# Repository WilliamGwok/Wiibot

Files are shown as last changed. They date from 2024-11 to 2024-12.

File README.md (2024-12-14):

### English Version Please Click: [ENG_README](https://github.com/WilliamGwok/Wiibot/blob/main/README_ENG.md)

### 日本語翻訳版: [JAP_README](https://github.com/WilliamGwok/Wiibot/blob/main/README_JAP.md)

# Wiibot

## 前言
<div align="center">
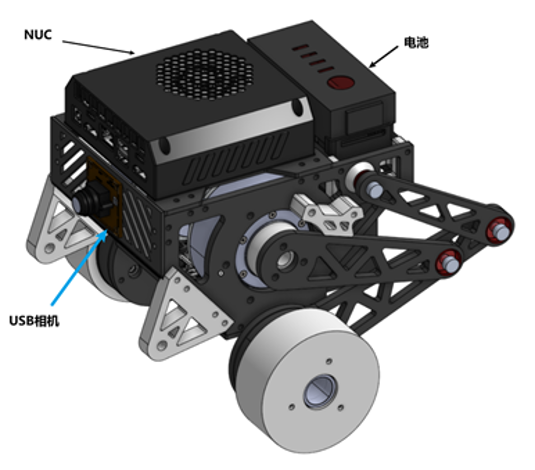
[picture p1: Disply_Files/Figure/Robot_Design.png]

</div>
<br>
<p align="center">本项目是选修机器人控制课程的课程设计，主要研究平衡车的控制与设计。该项目与先前的RP_Balance项目相似，但采用了不同的腿部构型，并保留了更多测试数据以支持研究分析。</p>
<p align="center">机器人机械部分由RobotPilots实验室的同事ZJH负责，视觉识别部分由ZZ负责。</p>

## 电控硬件清单
| 名称 | 部分技术参数 | 功能 | 数量 |
|---|---|---|---|
| Robomaster 开发板 C 型 | 输入电压: 8-28 V<br>IMU+E-compass: 1 个<br>CAN 总线接口: CAN1: 2 个; CAN2: 2 个<br>UART 接口: 2 个<br>SPI 接口: 1 个 | 搭载高性能芯片，支持机器人控制频率达 1000Hz，同时负责电机通讯、遥控信息接收及视觉模块通信。 | 1 |
| 迈克 mc6mini 遥控器航模接收机 | 通道数量: 6<br>频率范围: 2401-2478 MHz<br>控制范围: >800 m | 发送机器人平移、旋转、跳跃等动作指令。 | 1 |
| 领控 MG6012E-i8v3 伺服电机 | 额定电压: 48 V<br>空载转速: 310 rpm<br>额定扭矩: 6 Nm<br>峰值扭矩: 16 Nm | 控制机器人腿长及机体横滚角。 | 2 |
| Robomater GM6020 电机 | 额定电压: 24 V<br>空载转速: 320 rpm<br>额定扭矩: 1.2 Nm<br>峰值扭矩: 1.4 Nm  | 控制机器人驱动轮，实现平移、旋转及平衡。 | 2 |
| 经纬 M600 系列 TB47S 智能飞行电池 | 容量: 4500 mAh<br>电压: 22.2 V | 提供整套机器人的电控系统供电。 | 1 |
| DC-DC 可调电源模块 | 输入电压: 7-32 V<br>输出电压: 0-28 V<br>恒流范围: 0.2-1.2 A | 为视觉NUC提供稳定的工作电压与电流。 | 1 |

## 文件介绍

| 文件名 | 功能 | 文件链接 |
|---|---|---|
| Code | 包括MATLAB代码（建模求解、控制器设计、增益矩阵拟合、数据绘制）和实车代码（硬件驱动、通讯协议、模块控制与逻辑控制）。 | [CODE](https://github.com/WilliamGwok/Wiibot/tree/main/Code) |
| Display_Files | 机械、电控、视觉课程报告及演示文件。 | [DISPLAY](https://github.com/WilliamGwok/Wiibot/tree/main/Disply_Files) |
| Mec | 包含机器人机械设计图纸。 | [MEC](https://github.com/WilliamGwok/Wiibot/tree/main/Mec/balance) |
| Simulation | Webots平台的机器人仿真模型*。 | [SIM](https://github.com/WilliamGwok/Wiibot/tree/main/Simulation/webots) |
| Test_Video | 包含实车测试图片及视频文件。 | [VIDEO](https://github.com/WilliamGwok/Wiibot/tree/main/Test_Video) |

*由于导入STL文件到Webots平台较为复杂，简化模型后仿真世界仍难以正常运行。最终仅验证了机器人维持平衡的功能。

## 实车测试

对整车控制器性能进行了测试与分析。除腿长控制器和横滚角控制器的测试外，其他测试均在固定腿长的条件下进行。对应的增益矩阵K如下，所有数据通过J-Scope测量，并使用MATLAB绘制：

$$
K={\left[\begin{array}{l l l l l l}{-3.693}&{-3.287}&{-8.559}&{-0.591}&{3.693}&{0.369; }\\ {-3.693}&{-3.287}&{-8.559}&{-0.591}&{-3.693}&{-0.369}\end{array}\right]}
$$

### 平衡车位移、偏航角静态响应及俯仰角变化

在静止状态下，输入幅值为0.4的阶跃信号，测试机器人位移响应及俯仰角变化，结果如图1所示。

<div align="center">
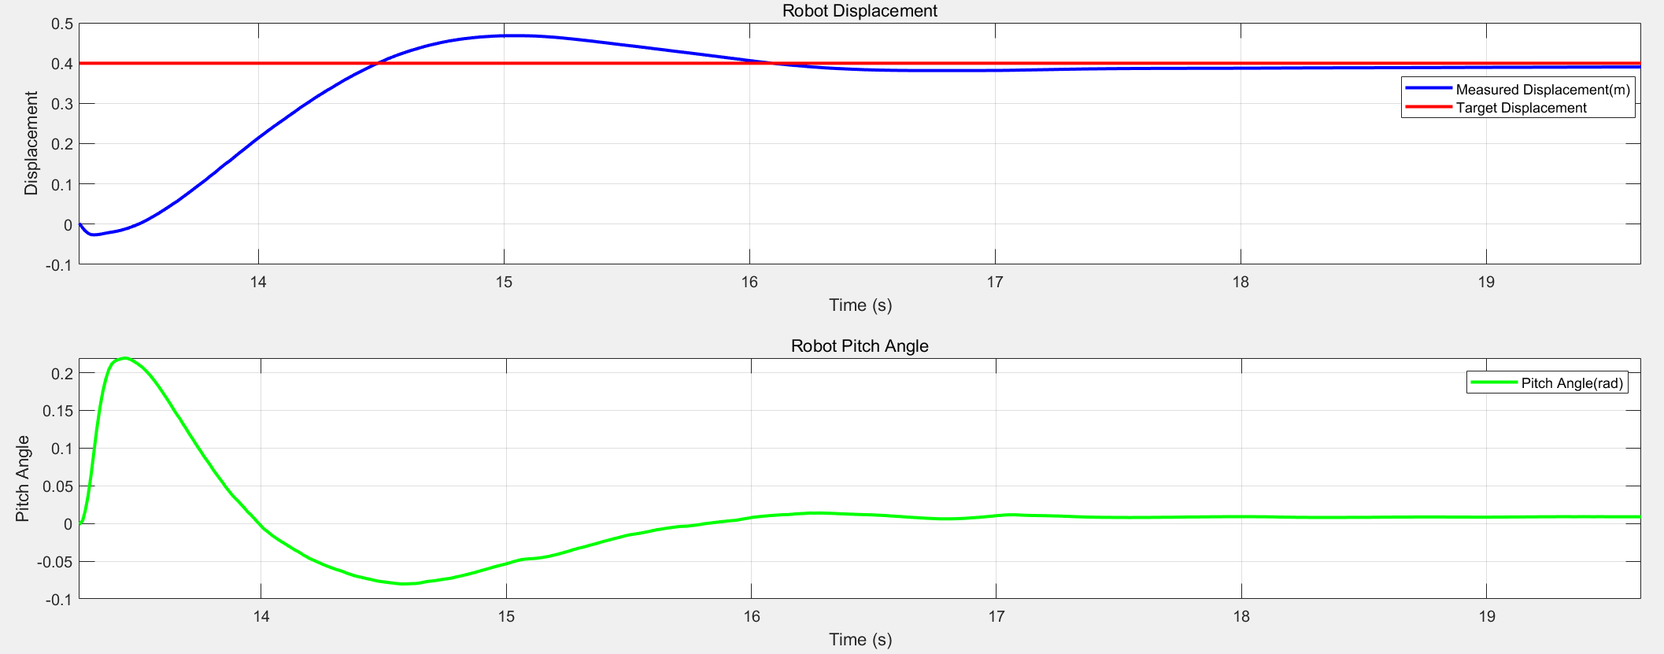
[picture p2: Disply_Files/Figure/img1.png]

</div>
<br>
<p align="center">图1 机器人位移阶跃响应及其俯仰角变化</p>

经测量，位移响应特性如下：

- 峰值时间 $T_{P}$：1.731s
- 超调量 $\upsigma\%$：17\%
- 调节时间 $T_{S}$（5%误差下）：2.542s

位移响应过程中，机器人最大俯仰角为0.219 rad（约12.549度）。

在静止状态下，输入幅值为1.579（约90度）的偏航角阶跃信号，测试偏航角响应及俯仰角变化，结果如图2所示。

<div align="center">
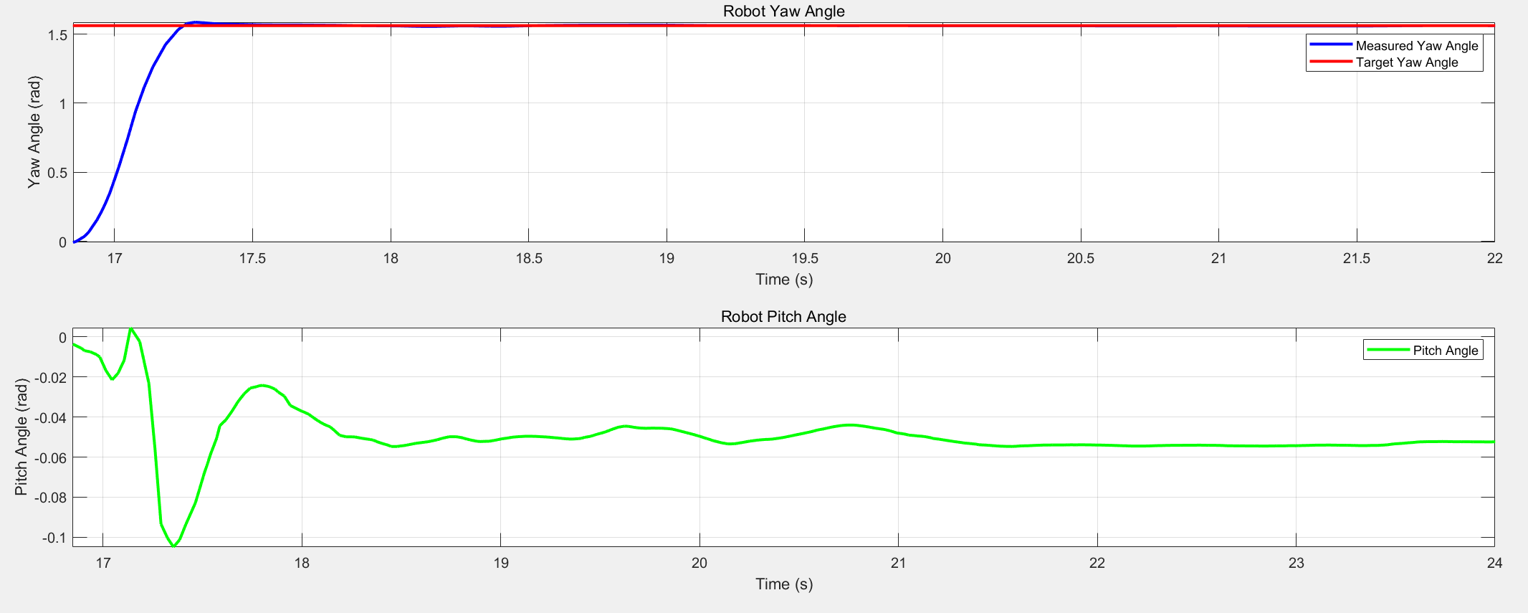
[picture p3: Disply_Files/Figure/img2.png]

</div>
<br>
<p align="center">图2 机器人偏航角阶跃响应及其俯仰角变化</p>

偏航角响应特性如下：

- 峰值时间 $T_{P}$：0.477s

- 超调量 $\upsigma\%$：1.6\%

- 调节时间 $T_{S}$（5%误差下）：0.385s

偏航角轨迹跟踪过程中，俯仰角在0.104 rad内产生小幅度震荡。

### 平衡车腿长及机体横滚角响应

采用双环PID控制器对腿长进行控制。输入幅值为0.3的阶跃信号，位置外环与速度内环响应如图3所示。

控制器参数如下：

$$
\begin{array}{l}{{K p=100,\qquad K i=0.5,\qquad I n t e r g r a l_{m a x}=10,\qquad O u t_{m a x}=30;}}\\ {{\mathrm{}}}\\ {{\mathrm{}\kappa p=0.4,\qquad K i=0.05,\qquad I n t e r g r a l_{m a x}=5,\qquad O u t_{m a x}=8;}}\end{array}
$$

<div align="center">
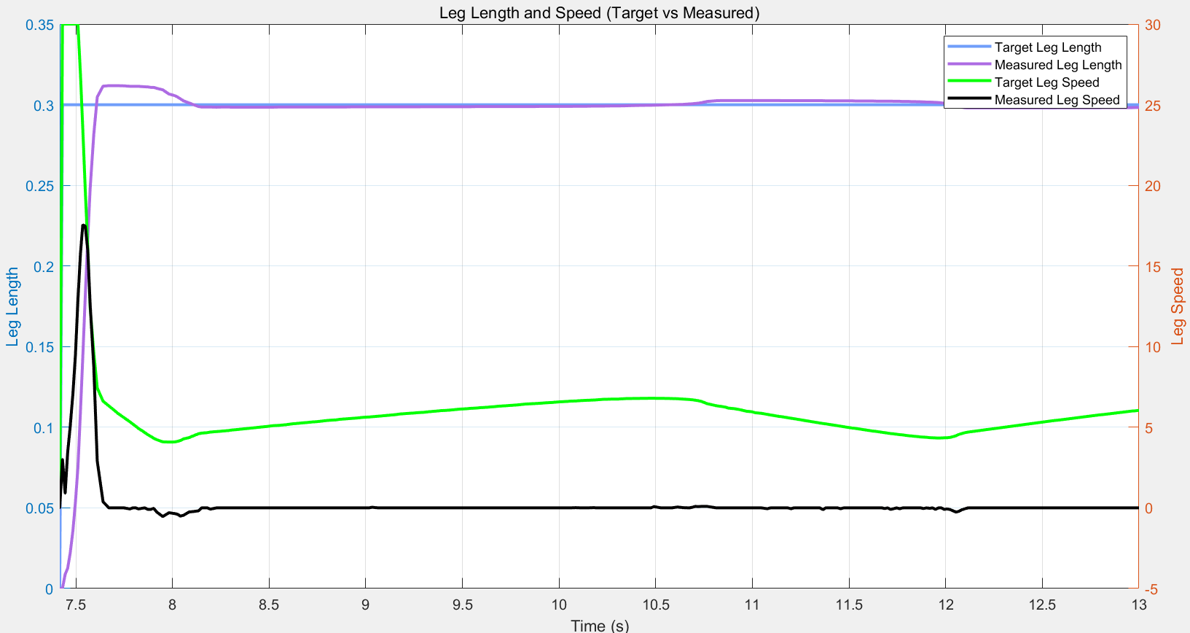
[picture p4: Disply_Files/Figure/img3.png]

</div>
<br>
<p align="center">图3 机器人腿长双环控制器响应</p>

再次输入最大腿长阶跃信号，响应如图4所示。

<div align="center">
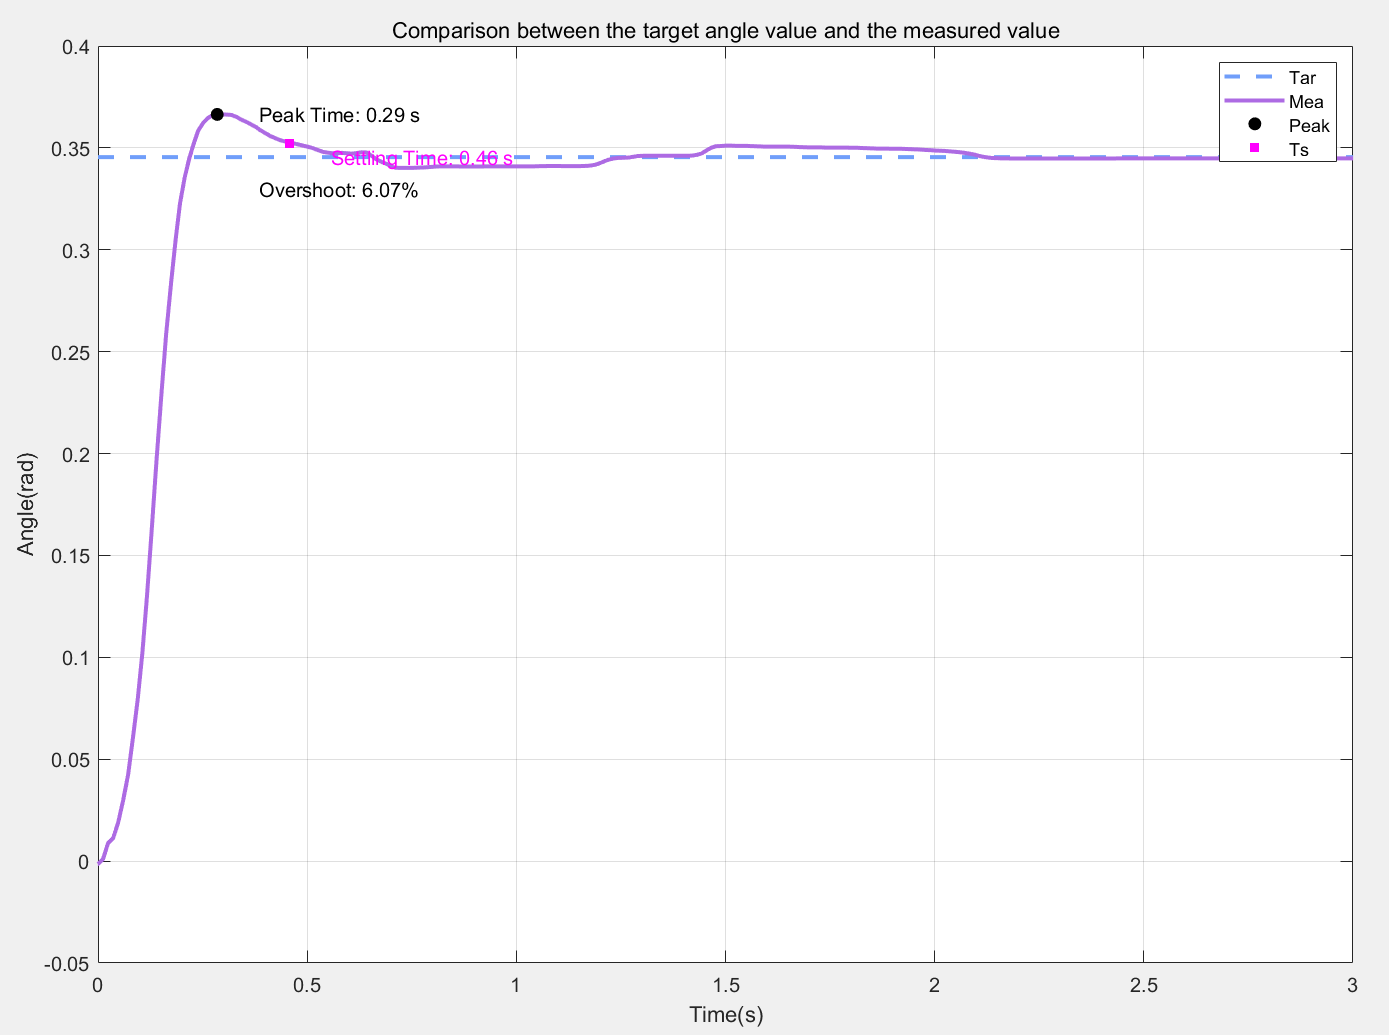
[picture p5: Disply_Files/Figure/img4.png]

</div>
<br>
<p align="center">图4 机器人腿长最大阶跃响应</p>

经测量，腿长响应特性如下：

- 峰值时间 $T_{P}$：0.29s

- 超调量 $\upsigma\%$：6.07\%

- 调节时间 $T_{S}$（2%误差下）：0.46s

横滚角响应通过单侧上坡动作*体现，其横滚角及左右腿腿长变化如图5所示。

<div align="center">
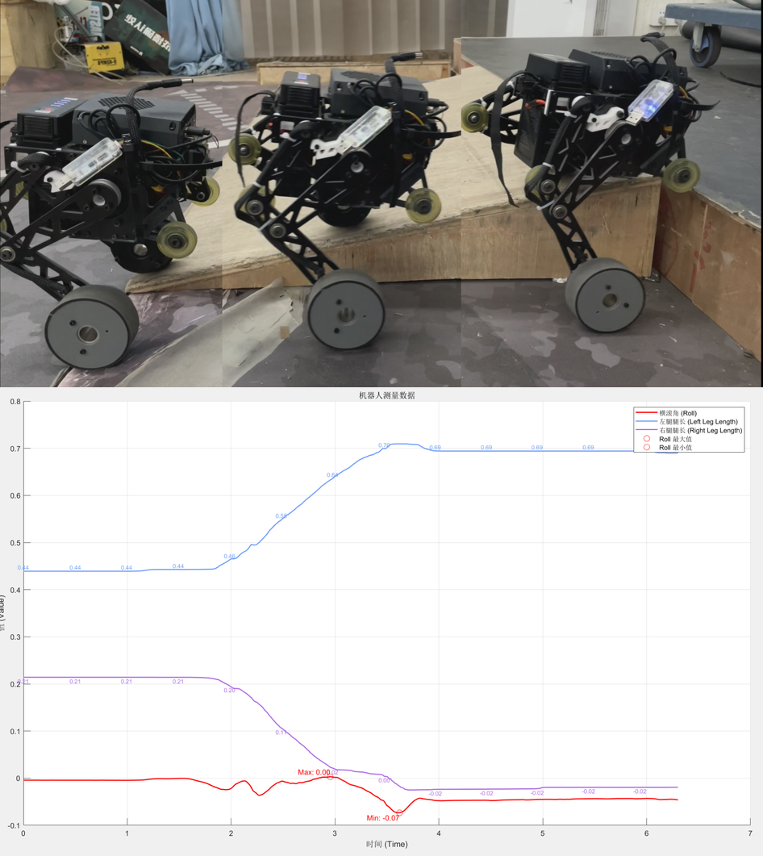
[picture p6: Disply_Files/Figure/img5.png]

</div>
<br>
<p align="center">图5 单侧上坡时横滚角与腿长变化</p>

*上坡过程持续2s，坡长约0.8m，坡度9 °

### 离地检测与跳跃动作

通过监测关节扭矩检测离地状态。图6展示了两次离地的关节扭矩输出曲线，设置离地阈值为0.5Nm，经测试可靠性较高。

<div align="center">
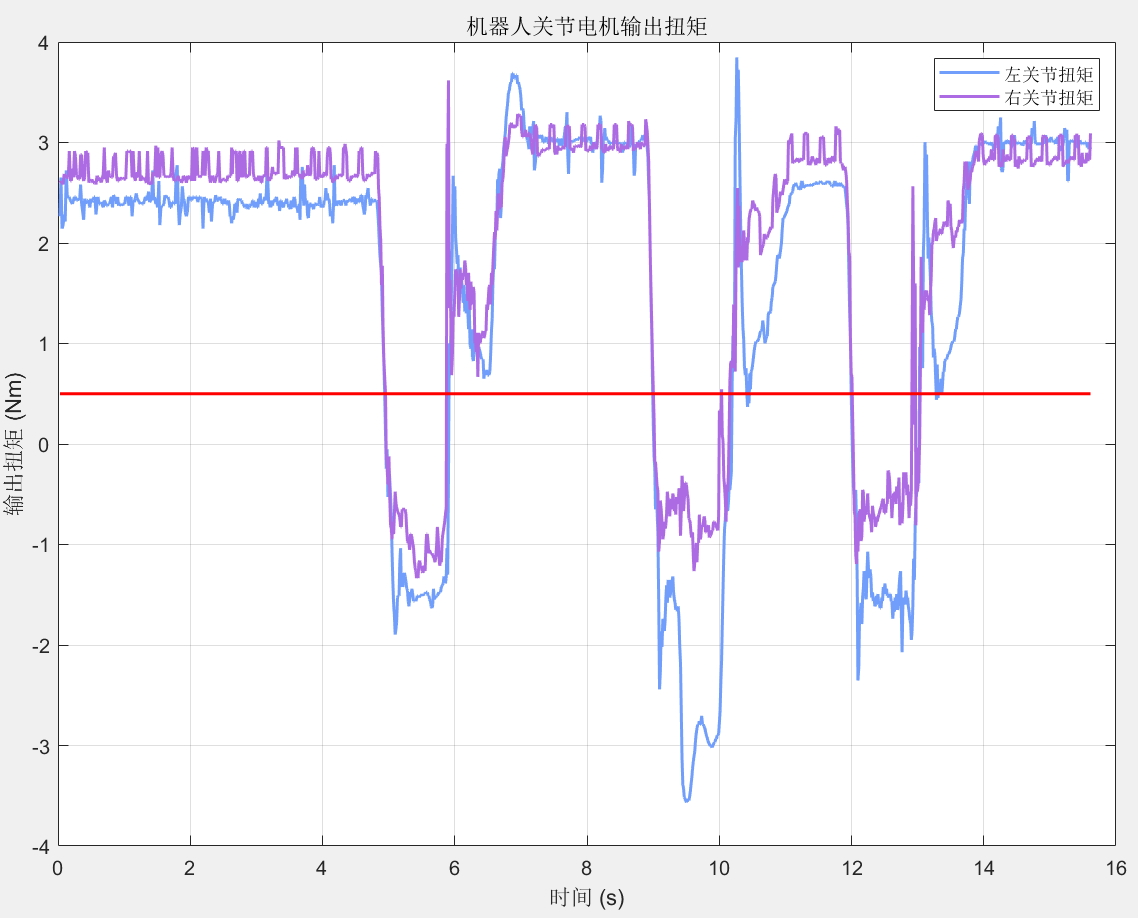
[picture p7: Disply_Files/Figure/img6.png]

</div>
<br>
<p align="center">图6 离地检测扭矩曲线</p>

通过给腿长输入大幅脉冲信号实现跳跃。平均跳跃高度约为0.1m，受限于电机性能，跳跃高度尚有改进空间。跳跃时的控制器输出如图7和图8所示。

<div align="center">
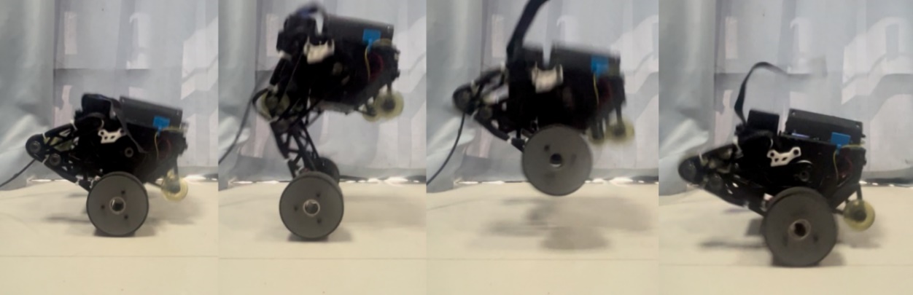
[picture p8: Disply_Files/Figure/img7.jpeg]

</div>
<br>
<p align="center">图7 跳跃过程</p>

<div align="center">
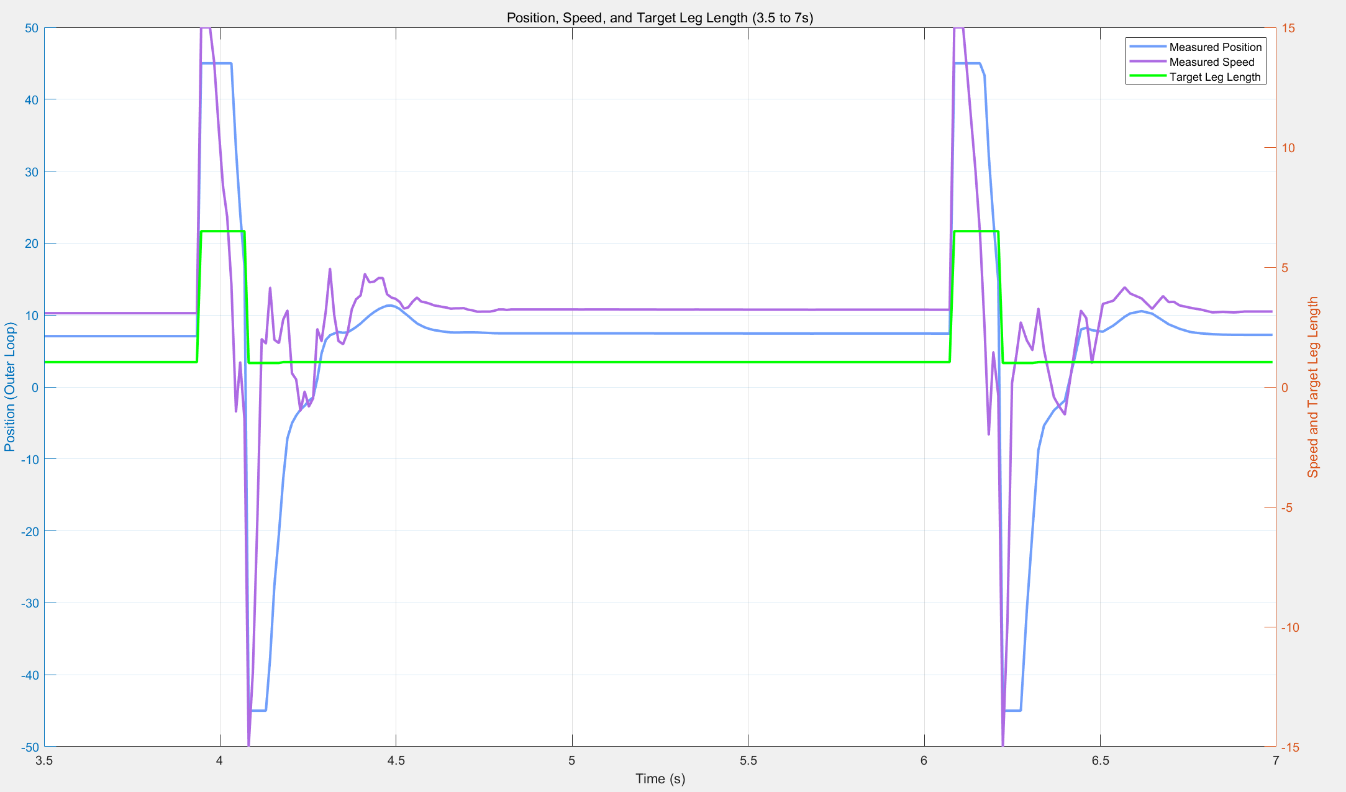
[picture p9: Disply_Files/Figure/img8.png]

</div>
<br>
<p align="center">图8 跳跃动作控制器输出曲线</p>

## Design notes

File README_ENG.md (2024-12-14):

# Wiibot

## Preface
<div align="center">

</div>
<br>
<p align="center">This project is part of the coursework for the Robotics Control course, focusing on the control and design of a balance robot. It is similar to the previous RP_Balance project but adopts a different leg configuration and retains more test data to support research and analysis.</p>
<p align="center">The mechanical components of the robot were designed by ZJH from the RobotPilots lab, while the visual recognition module was handled by ZZ.</p>

## Electronic Hardware List
| Name | Technical Specifications | Function | Quantity |
|---|---|---|---|
| Robomaster Development Board Type C | Input Voltage: 8-28 V<br>IMU+E-compass: 1<br>CAN Bus: CAN1: 2 ports; CAN2: 2 ports<br>UART Ports: 2<br>SPI Port: 1 | Supports high-performance chip with control frequency up to 1000Hz; handles motor communication, remote control signal reception, and vision module communication. | 1 |
| Mike MC6mini Remote Control Receiver | Channels: 6<br>Frequency Range: 2401-2478 MHz<br>Control Range: >800 m | Sends commands for robot translation, rotation, and jumping actions. | 1 |
| Lingkong MG6012E-i8v3 Servo Motor | Rated Voltage: 48 V<br>No-load Speed: 310 rpm<br>Rated Torque: 6 Nm<br>Peak Torque: 16 Nm | Controls leg length and robot body roll angle. | 2 |
| Robomater GM6020 Motor | Rated Voltage: 24 V<br>No-load Speed: 320 rpm<br>Rated Torque: 1.2 Nm<br>Peak Torque: 1.4 Nm | Drives the robot wheels for translation, rotation, and balance. | 2 |
| DJI M600 TB47S Intelligent Flight Battery | Capacity: 4500 mAh<br>Voltage: 22.2 V | Provides power for the entire robot control system. | 1 |
| DC-DC Adjustable Power Module  | Input Voltage: 7-32 V<br>Output Voltage: 0-28 V<br>Constant Current Range: 0.2-1.2 A | Supplies stable voltage and current to the vision NUC. | 1 |

## File Overview

| Filename | Function | File Link |
|---|---|---|
| Code | Includes MATLAB code (modeling, controller design, gain fitting, data plotting) and real robot code (hardware drivers, communication protocols, module control, and logic control). | [CODE](https://github.com/WilliamGwok/Wiibot/tree/main/Code) |
| Display_Files  | Reports and presentation files on mechanics, electronics, and vision. | [DISPLAY](https://github.com/WilliamGwok/Wiibot/tree/main/Disply_Files) |
| Mec | Contains mechanical design drawings of the robot. | [MEC](https://github.com/WilliamGwok/Wiibot/tree/main/Mec/balance) |
| Simulation | Robot simulation models for the Webots platform.* | [SIM](https://github.com/WilliamGwok/Wiibot/tree/main/Simulation/webots) |
| Test_Video | Includes real robot test images and videos. | [VIDEO](https://github.com/WilliamGwok/Wiibot/tree/main/Test_Video) |

*Due to the complexity of importing STL files into the Webots platform, the simplified model still struggled to function properly in the simulation environment. Only balance maintenance was verified.

## Real Robot Tests

The performance of the overall controller was tested and analyzed. Except for the leg length controller and roll angle controller tests, other tests were conducted under fixed leg length conditions. The corresponding gain matrix K is shown below. All data was measured with J-Scope and plotted using MATLAB:

$$
K={\left[\begin{array}{l l l l l l}{-3.693}&{-3.287}&{-8.559}&{-0.591}&{3.693}&{0.369; }\\ {-3.693}&{-3.287}&{-8.559}&{-0.591}&{-3.693}&{-0.369}\end{array}\right]}
$$

### Balance Robot Displacement, Yaw Angle Static Response, and Pitch Angle Variation

In a stationary state, an input step signal with an amplitude of 0.4 was applied to test the robot's displacement response and pitch angle variation. The results are shown in Figure 1.

<div align="center">

</div>
<br>
<p align="center">Figure 1 Displacement Step Response and Pitch Angle Variation</p>

The measured displacement response characteristics are as follows:

- Peak Time $T_{P}$: 1.731s
- Overshoot $\upsigma\%$: 17%
- Settling Time $T_{S}$ (within 5% error): 2.542s

During the displacement response, the maximum pitch angle was 0.219 rad (approximately 12.549 degrees).

Under stationary conditions, an input yaw step signal with an amplitude of 1.579 (approximately 90 degrees) was applied to test the yaw response and pitch angle variation. The results are shown in Figure 2.

<div align="center">

</div>
<br>
<p align="center">Figure 2 Yaw Step Response and Pitch Angle Variation</p>

Yaw response characteristics are as follows:

- Peak Time $T_{P}$: 0.477s

- Overshoot $\upsigma\%$: 1.6%

- Settling Time $T_{S}$ (within 5% error): 0.385s

During yaw trajectory tracking, the pitch angle oscillated slightly within 0.104 rad.

### Balance Robot Leg Length and Body Roll Angle Response

A dual-loop PID controller was used for leg length control. When a step signal with an amplitude of 0.3 was applied, the outer position loop and inner velocity loop responses are shown in Figure 3.

Controller parameters:

$$
\begin{array}{l}{{K p=100,\qquad K i=0.5,\qquad I n t e r g r a l_{m a x}=10,\qquad O u t_{m a x}=30;}}\\ {{\mathrm{}}}\\ {{\mathrm{}\kappa p=0.4,\qquad K i=0.05,\qquad I n t e r g r a l_{m a x}=5,\qquad O u t_{m a x}=8;}}\end{array}
$$

<div align="center">

</div>
<br>
<p align="center">Figure 3 Leg Length Dual-Loop Controller Response</p>

When the maximum leg length step signal was applied, the response is shown in Figure 4.

<div align="center">

</div>
<br>
<p align="center">Figure 4 Maximum Leg Length Step Response</p>

The measured leg length response characteristics are as follows:

- Peak Time $T_{P}$: 0.29s

- Overshoot $\upsigma\%$: 6.07%

- Settling Time $T_{S}$ (within 2% error): 0.46s

The roll angle response was demonstrated through a single-side uphill motion*, with the roll angle and left/right leg length variations shown in Figure 5.

<div align="center">

</div>
<br>
<p align="center">Figure 5 Roll Angle and Leg Length Variation During Single-Side Uphill</p>

*The uphill process lasted 2 seconds, with a slope length of approximately 0.8m and a slope angle of 9°.

### Ground Detection and Jumping Motion

Ground detection was achieved by monitoring joint torque. Figure 6 shows the torque curves for two ground detections. The threshold was set at 0.5 Nm, with high reliability observed during tests.

<div align="center">

</div>
<br>
<p align="center">Figure 6 Torque Curves for Ground Detection</p>

Jumping was implemented by inputting a large pulse signal to the leg length. The average jump height was approximately 0.1m. Limited by motor performance, the jump height has room for improvement. The controller outputs during jumping are shown in Figures 7 and 8.

<

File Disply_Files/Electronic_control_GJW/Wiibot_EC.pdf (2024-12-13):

深圳大学本科生生课程论文

1.系统建模

对于机器人的平衡，纵向以及转向运动，可以将模型简化为三维空间中的类一阶倒立摆 模型，即忽略腿长的变化，转向运动由两个驱动轮差速运动控制。

1.1 模型定义

称机器人机体质心到两个驱动轮转轴中心的连线为摆杆，得到如图 1 所示平衡车 模型。

该模型的变量与参数定义如表 1、表 2 所示。

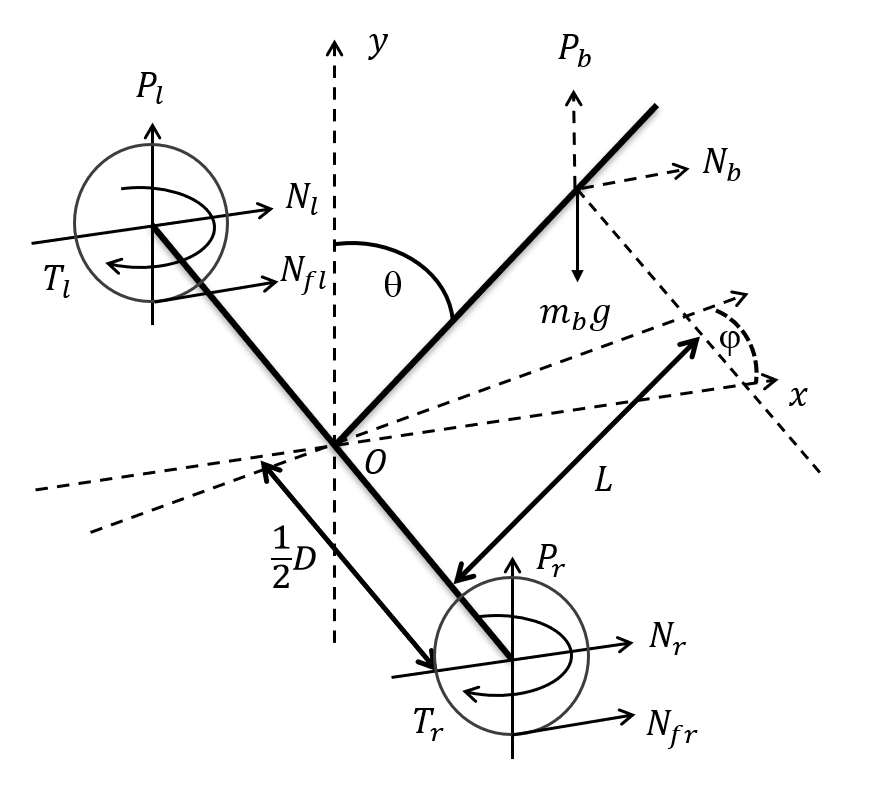
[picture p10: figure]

图 1 平衡车模型

表 1 平衡车模型变量定义

符号 | 含义 | 正方向 | 单位
θ | 摆杆与竖直方向夹角 | 图示为正方向 | rad
φ | 摆杆偏航角 | 图示为正方向 | rad
xi | 驱动轮位移 | X 轴正方向 | m
xb | 机体位移 | X 轴正方向 | m
Pi | 驱动轮对摆杆力的竖直分量 | 箭头所示 | N
Pb | 摆杆受到的竖直方向力 | 箭头所示 | N
Ni | 驱动轮对摆杆力的水平分量 | 箭头所示 | N

Nb | 摆杆受到的水平方向力 | 箭头所示 | N
Ti | 驱动轮输出力矩 | 箭头所示 | N·m

表 2 平衡车模型参数定义

符号 | 单位 | 含义
D | m | 车体转向直径
R | m | 驱动轮半径
L | m | 摆杆质心到驱动轮转轴中心的直线长度
mw | kg | 驱动轮质量
mb | kg | 摆杆质量
Ib | kg ∙ m² | 摆杆绕质心关于 Z 轴的转动惯量
Iw | kg ∙ m² | 驱动轮转子转动惯量
Iz | kg ∙ m² | 整车质心关于 Y 轴的转动惯量

1.2 经典力学分析

对驱动轮，有：

mwxi

̈ = Nfi − Ni | (1)

Iw

xi

̈
R
= Ti − NfiR | (2)

对摆杆，有：

mbxb̈ = Nfl + Nfr | (3)
mbyb̈ = Pr + Pl − mbg | (4)

Ibθb

̈ = (Pr + Pl)L sin θb − (Nr + Nl )L cos θb − (Tr + Tl) | (5)

对整车，有：

Izφ̈=

D
2
(Nl − Nr ) | (6)

其中：

xb = x + L sin θb | (7)
yb = L cos θb | (8)

1.3 状态空间模型

定义非线性模型：

ẋ = f(x, Tl

, Tr )

利用 MATLAB 符号运算工具，联立式（1）到式（8），通过函数 solve 对方程组消 去中间变量，最终得到非线性表达式（9），式（10），和式（11）

2mwẍ+ mb (ẍ− L (sin(θb) θb
̇

2
− θb

̇ cos(θb))) −

Tl
R

−

Tr
R

+

2Iwẍ
R²
= 0 | (9)

Tl + Tr + Ibθb

̈ − L sin(θb) (gmb − Lmb (cos(θb) θb ̇

2
+ θb

̈ sin(θb))) − 2Lmwẍcos(θb)

+

LTl cos(θb)
R

+

LTr ∗ cos(θb)
R

−

2IwLẍcos(θb)
R²
= 0 | (10)

DTlR = mwφb

̈D
2R

2 + Iwφb

̈D
2 + TrDR + 2Izφb

̈R
2 | (11)

定义状态向量 x 与控制向量 u 分别为：

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
φ̇ ]

, u = [

Tl
Tr

]

根据式状态向量 x 与控制向量 u，求非线性模型在平衡点处的雅可比矩阵并对其线性化，即 将θ = 0，则sin θ = θ, cos θ = 1代入式（9）到（11）后，求：

A =

∂f
∂x (x, u), B =

∂f
∂u (x, u)

其中，x、u 是系统平衡点，即方程f(x, u) = 0的解：

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
, u = [

0/0]

最终求得的状态方程为：

ẋ =
[
0 1 | 0 | 0 | 0 0
0 0 A1 | A2 | 0 0
0 0 | 0 | 1 | 0 0
0 0 A3 | A4 | 0 0
0 0 | 0 | 0 | 0 1
0 0 | 0 | 0 | 0 0]

x +
[
0 | 0
B1 | B2
0 | 0
B3 | B4
0 | 0
B5 | B6]
u | (12)

由于表达式略为复杂，此处用符号代替，具体内容可通过运行 MATLAB 代码在工作空间中 查看。

所有变量均可通过平衡车上各个传感器（如驱动轮编码器，IMU 模块等）直接测量或通过数 据融合解算得到，故可得系统输出y = I6x，其中I6为单位阵。

代入平衡车实车模型参数后可以得到该状态空间模型的状态矩阵 A 和控制矩阵 B，在 MATLAB 中使用 rank 函数求得其可控矩阵满秩，系统可控。系统输出矩阵 C 为单位矩阵， 系统可观。

1.4 仿真验证

将 Solidwork 中搭建的模型分模块导入到仿真软件 Webots 中，通过对关节电机设置其允许 位移为 0，得到一个定腿长的平衡车模型。

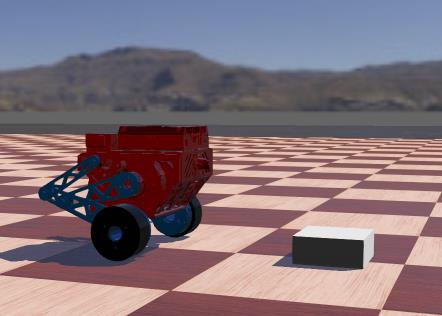
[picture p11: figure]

图 2 仿真环境中的整车模型

通过使用 MATLAB 中的 lqr 函数计算得到反馈增益矩阵 K。因为在仿真中主要目的是验证 模型建立是否正确，用于计算 K 矩阵的 Q 和 R 权矩阵的数值选取只关注机器人俯仰角的稳 定。经检验，得到模型正确。

2 控制器设计

基于本项目的平衡车构型，除了机器人的平移、转向和保持平衡的控制外，还需要控制 平衡车双腿的长度及其横滚角。

2.1 LQR 控制器

基于上述求得的状态空间方程，通过一个 LQR 控制器可以较好地对机器人平移、旋转 以及机体俯仰角进行控制。

设计控制律为系统状态的线性组合：

u = −Kx = − [

K11 | K12 | K13 | K14 | K15 | K16
K21 | K22 | K23 | K24 | K25 | K26

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
φ̇ ]

通过线性二次型调节器计算反馈矩阵，定义代价函数为

J = ∫ (x
TQx + u

TRu)dt

∞

0
其中：
- x 是系统状态向量；
- u是控制输入向量；
- Q 是对状态变量的加权矩阵，通常是半正定矩阵，反映了对状态偏离的惩罚；
- R是对控制输入的加权矩阵，通常是正定矩阵，反映了对控制能量的惩罚。

最优控制律：

为了使代价函数J达到最小，控制输入 u 应满足以下关系：

u = −R

−1B

TPx

其中：

- P是代数 Riccati 方程的解。

反馈增益矩阵：

通过上述控制律，反馈增益矩阵 K可以表示为：

K = R

−1B

TP

代数 Riccati 方程:

矩阵P需要满足以下代数 Riccati 方程：

A

TP + PA − PBR

−1B

TP + Q = 0

其中：

- A 和 B 是系统状态空间方程中的系统矩阵和输入矩阵。

为了可以控制平衡车的移动和转向，还需要实现对位移和偏航角两个状态变量的轨迹跟 踪。在系统输入中加入参考输入，即状态期望：

u = −K(x − xd)

其中xd为：

xd =
[

xd
0
0
0
φd
0 ]

xd为期望位移，φd为期望偏航角，两者均由其期望一阶微分量对时间积分得到。

2.2 双环 PID 控制器

基于该项目平衡车的四连杆腿部构型，可以通过关节电机的输出来调整机器人的腿部长 度；同时，为了让机器人在进行视觉识别时机体保持横滚角水平，还需要根据机器人实时的 横滚角值来调整两边腿的长度。

为了让机器人的腿长控制有更快的响应速度和鲁棒性，引入两个双环 PID 控制器分别 对机器人的腿长和横滚角进行控制，最后并行输出到电机控制电流值。

腿长的控制框图如图 3 所示：

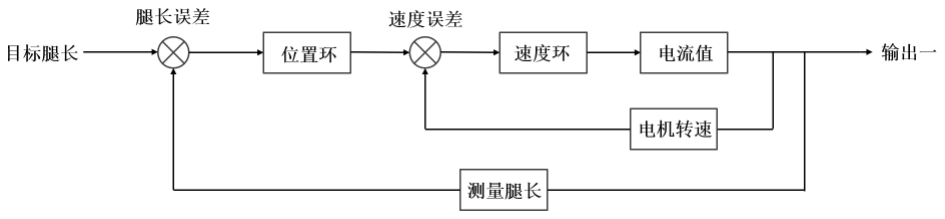
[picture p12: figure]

图 3 机器人腿长双环 PID 控制框图

横滚角的控制框图如图 4 所示：

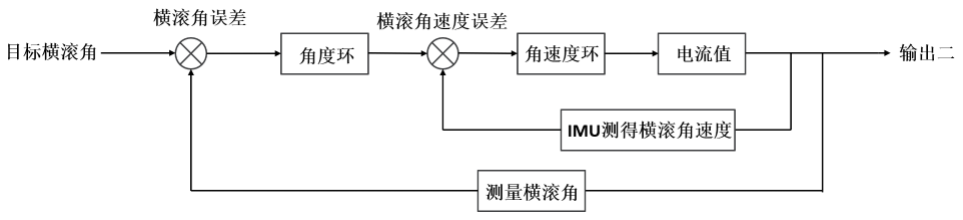
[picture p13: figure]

图 4 机器人横滚角双环 PID 控制框图

最终发送的电机电流值为两个控制器的输出之和。

2.3 增益矩阵 K 的参数拟合

在建模阶段，我们将倒立摆的杆长假设为定值，但实际上，该值会随着机器人腿长的变 化而改变，其对应的模型也会有差异。由于求得解析解较为困难，我们将机器人腿长作为拟 合的自变量，对增益矩阵 K 进行四阶多项式拟合。

由于实车环境下我们无法直接测量机器人实时腿长，需要由一些角度关系推算得到。将 模型简化至如图 5 所示。

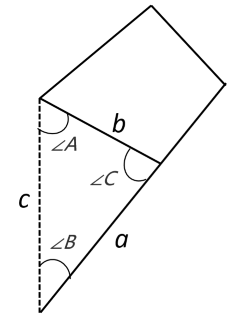
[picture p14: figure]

图 5 腿部四连杆结构简化模型

其中，三角形边 a、边 b 可以通过在机械图纸中测量得到，角 A 可以由电机编码器求 得，边 c 则是期望求得的机器人腿长。由余弦定理得式（13）：

a

2 − b

2 − c

2 + 2bc cos(A) = 0 | (13)

通过 MATLAB 的 solve 函数求解（排除负数解）得式（14）：

c = b cos(A) + √a
2 + b

2 cos²(A) − b

2 | (14)

经测量，实车边b = 0.11291m，边a = 0.11461m，将数据代入并由 0 至 90 度遍历角 A 可以得到角 A 与腿长的关系曲线如图 6 所示。

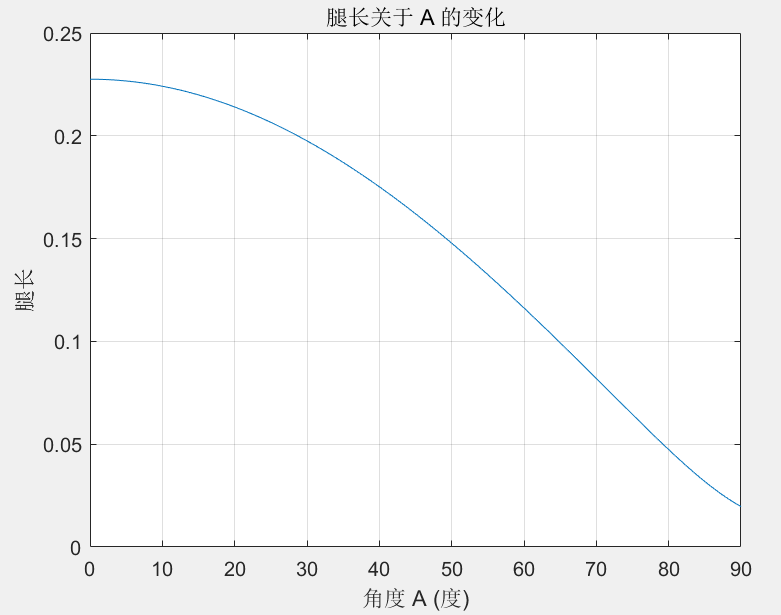
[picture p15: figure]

图 6 机器人腿长与角度 A 的关系曲线

在 MATLAB 中遍历腿长，计算不同腿长值下的增益矩阵 K，并对 K 矩阵每个元素进 行关于角度 A 的多项式拟合，求得拟合系数并存到 EXCEL 表格中，以便将它们添加进实 车代码中进行增益矩阵的实时计算。

拟合公式如式（15）：

y = a4x

4 + a3x

3 + a2x

2 + a1x + a0

其中 y 对应 K 矩阵的各个元素，x 为测得角度 A 的值。

最终的拟合效果如图 7 所示，蓝色曲线为各个角度 A 值下的实际 K 矩阵值，紫色曲线 为拟合值。

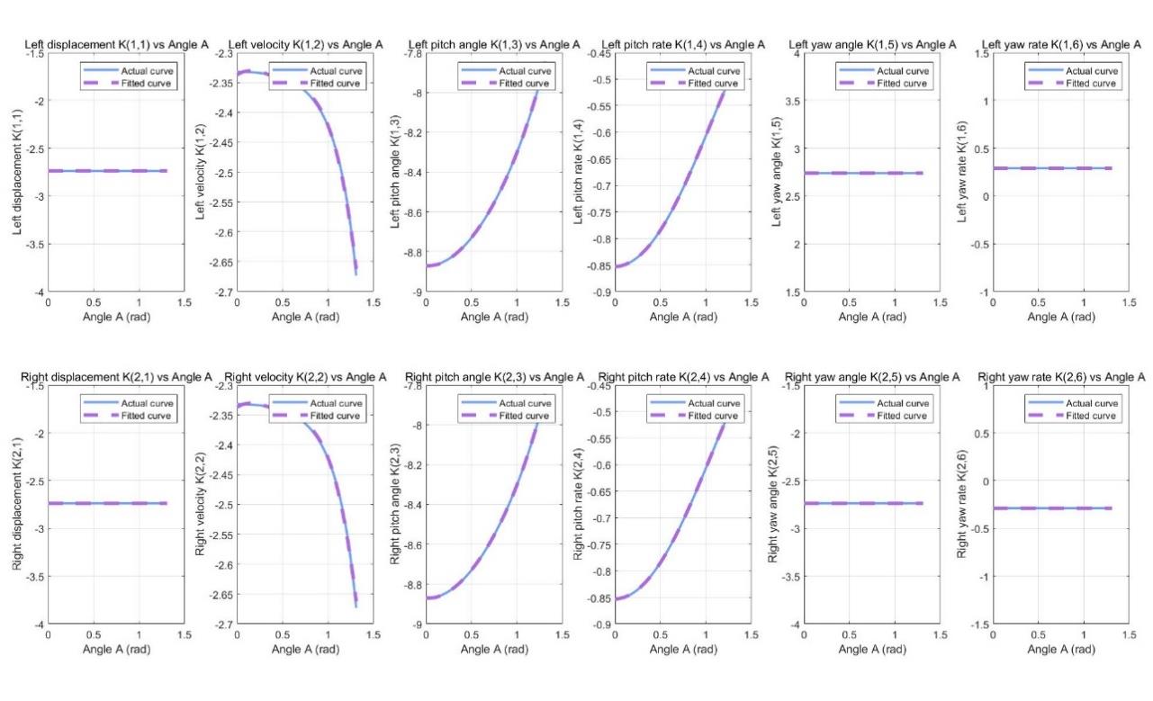
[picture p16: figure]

图 7 增益矩阵 K 的实际曲线与拟合曲线对比

通过对比，可知拟合效果满足实车控制需求。

3. 实车硬件选型及代码框架介绍

基于项目需求及材料储备，本次选取的电控硬件型号如表 3 所示。

表 3 平衡车实车主要电控硬件表

名称 | 部分技术参数 | 功能 | 数量
Robomaster 开发板 C 型 | 输入电压：8-28 V IMU+E-compass：1 个 CAN 总线接口：CAN1：2 个；CAN2：2 个 UART 接口：2 个 SPI 接口：1 个 | 搭载的芯片提供足够高的运算能 力，让机器人控制频率保持 1000Hz。电机通讯、遥控器信息接 收以及视觉电脑通讯 | 1
迈克 mc6cmini 遥控器航模 接收器接收机 | 通道数量：6 频率范围：2401-2478 Mhz 控制范围：>800 m | 发送摇杆值，发送机器人平移、旋 转、跳跃等指令 | 1
瓴控 MG6012E-i8v3 伺服电 机 | 额定电压：48 V 空载转速：310 rpm 额定扭矩：6 Nm 峰值扭矩：16 Nm | 机器人关节电机，控制机器人的腿 长以及机体横滚角 | 2
Robomater GM6020 电机 | 额定电压：24 V 空载转速：320 rpm 额定扭矩：1.2 Nm 峰值扭矩：1.4 Nm | 机器人驱动轮电机，执行平移、旋 转、维持平衡等动作 | 2
经纬 M600 系列 TB47S 智 能飞行电池 | 容量: 4500 mAh 电压: 22.2 V | 整套机器人电控系统的供电 | 1
DC-DC 可调电源模块 | 输入电压：7-32 V 输出电压：0.8-28 V 恒流范围：0.2-12 A | 为视觉电脑提供适配的工作电压及 电流 | 1

4. 实车测试结果与数据分析

对整车多个控制器的控制效果进行分析，除了腿长控制器和横滚角控制器的测试，所有数据 测量均在固定腿长的实车状态下测得，对应的增益矩阵 K 如下所示。数据均在 J-Scope 中测 得，在 MATLAB 中绘制。

K = [

−3.693 −3.287 −8.559 −0.591 | 3.693 | 0.369
−3.693 −3.287 −8.559 −0.591 −3.693 −0.369]

4.1 平衡车位移、偏航角静态响应及俯仰角变化

在静止状态下，给机器人位移期望输入幅值为0.4的阶跃信号，其位移响应及俯仰角变 化如图 8 所示。

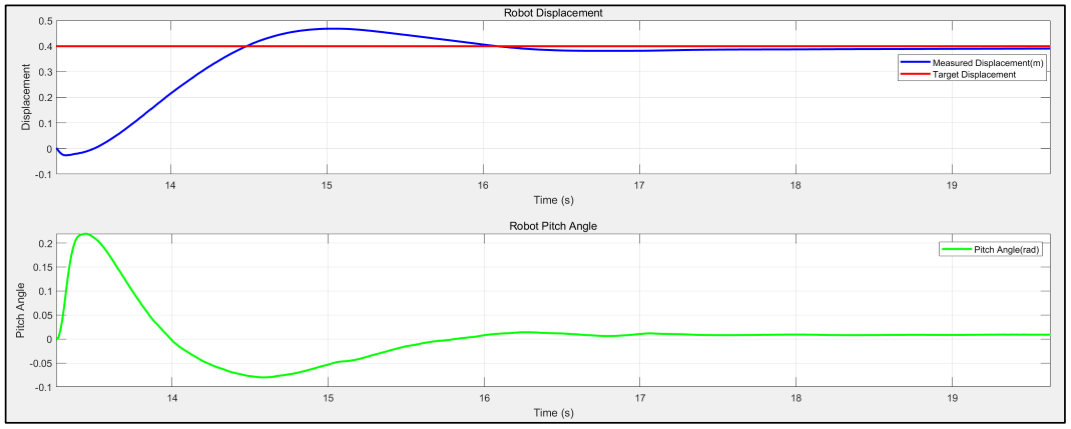
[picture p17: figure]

图 8 机器人位移阶跃响应及其过程俯仰角变化

经测量，位移响应的峰值时间TP为：

TP = 1.731s

超调量σ%为：

σ% =

Amax − Asteady

Asteady

× 100% =

0.468 − 0.400
0.4

× 100% = 17%

调节时间TS为（5%误差下）：

TS = 2.542s

在位移状态量的轨迹跟踪过程中，测得机器人机体最大俯仰角为0.219 rad，即约 12.549 度。

在静止状态下，给机器人偏航角期望输入幅值为1.579（约 90 度）的阶跃信号，其偏航 角响应及俯仰角变化如图 9 所示。

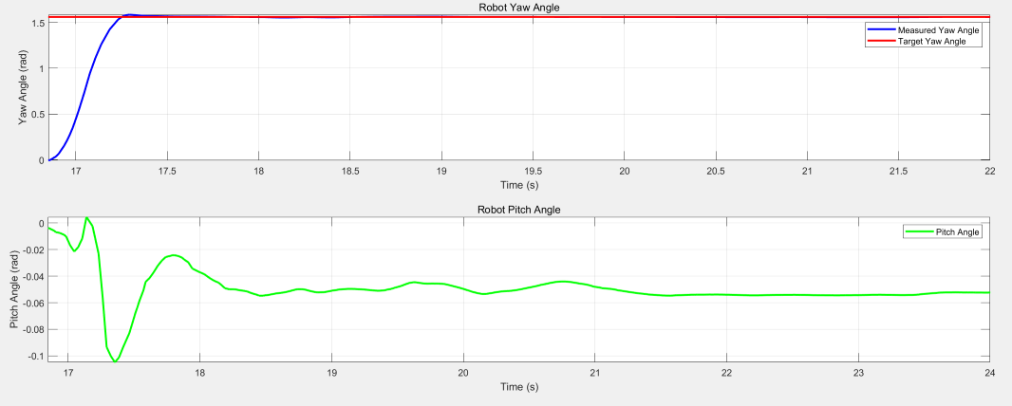
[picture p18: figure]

图 9 机器人偏航角阶跃响应及其过程俯仰角变化

经测量，位移响应的峰值时间TP为：

TP = 0.477s

超调量σ%为：

σ% =

Amax − Asteady

Asteady

× 100% =

1.585 − 1.560
1.560 × 100% = 1.6%

调节时间TS为（5%误差下）：

TS = 0.385s

在偏航角状态量的轨迹跟踪过程中，测得机器人机体俯仰角在转动过程中会在 0.104 rad内产生小幅度震荡。

综上，机器人位移响应速度较慢，考虑到测量过程中没有加入机器人速度状态的轨迹跟 踪，且响应过程中机体倾角较小，实际响应效果可以满足项目需求。偏航角的响应十分迅速， 且超调量小，对机体的俯仰角影响十分有限，也能满足项目需求。

4.2 平衡车腿长及机体横滚角响应

对于机器人腿长的控制，我们采用了双环 PID 控制器。对腿长目标值输入幅值为 0.3 的 阶跃信号。其位置外环及速度内环的响应曲线如图 10 所示。

其中，该 PID 控制器的内外环参数如下所示：

位置环外环：Kp = 100, | Ki = 0.5, | Intergralmax = 10, | Outmax = 30;
速度环外环：Kp = 0.4, | Ki = 0.05, | Intergralmax = 5, | Outmax = 8;

基于关节电机的扭矩参数，额定扭矩为6N ∙ m，峰值扭矩为16N ∙ m，设置常态下速度环 的最大速出为 8，即8N ∙ m。

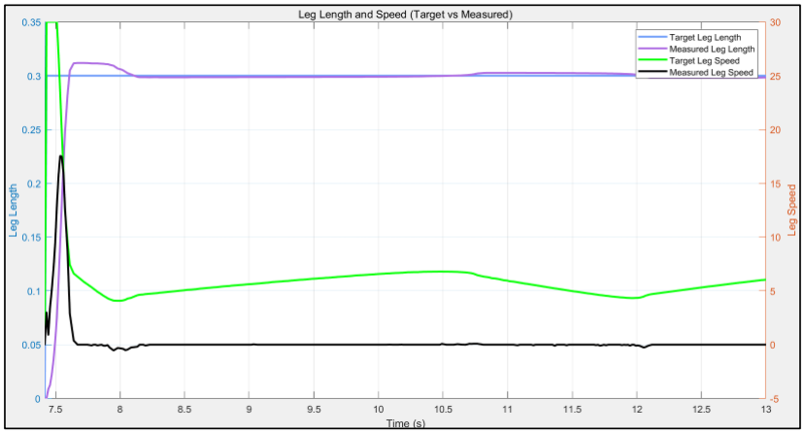
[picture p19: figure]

图 10 机器人腿长双环控制器的内外环响应曲线

由图 10 可以看到，速度响应在初始阶段有一段锯齿波形，这是由于机械的腿部涉及有 一些干涉导致的。再次输入阶跃信号，其幅值为机器人的最高腿长，其响应曲线如图 11 所 示。

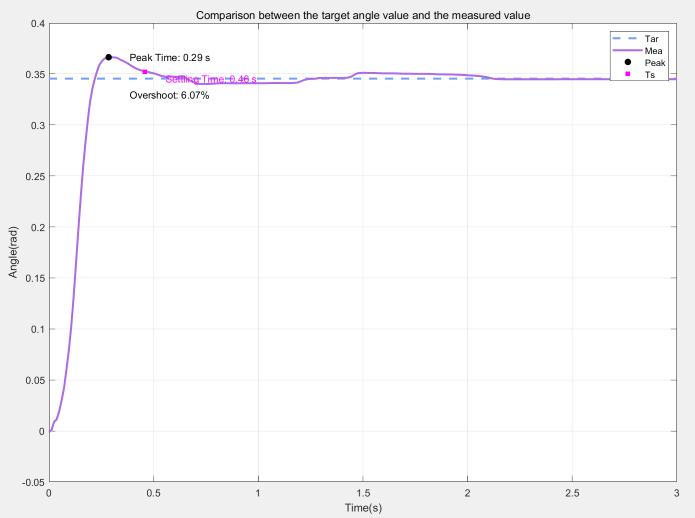
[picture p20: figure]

图 11 机器人腿长最大阶跃响应曲线

经测量，腿长响应的峰值时间TP为：

TP = 0.29s

超调量σ%为：

σ% =

Amax − Asteady

Asteady

× 100% =

0.366 − 0.350
0.350 × 100% = 6.07%

调节时间TS为（2%误差下）：

TS = 0.46s

关于机器人横滚角的响应，我们通过让机器人完成单侧上坡的动作来体现。其上坡过程 中的横滚角变化曲线及左右腿腿长变化曲线如图 12 所示。

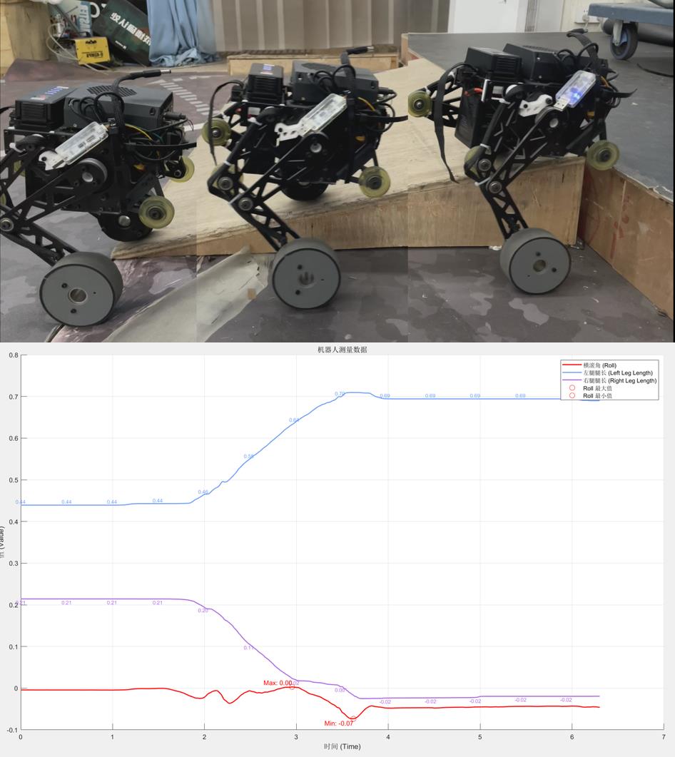
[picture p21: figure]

图 12 机器人单侧上坡时测得的机体横滚角和两腿长度

由图 12 可以得到，在单侧上坡过程中，通过横滚角 PID 控制器控制双边腿长发生改变， 来使得机体始终保持横滚角为 0。由测得数据可知，该过程中机器人横滚角的变化幅值为 0 到 0.07 rad，该横滚角响应性能满足项目需求。

4.3 离地检测与跳跃动作

在机器人跳跃过程中，机器人整体会完全离开地面，此时其模型与在地面时有差异， 这将会导致系统发散。故高效的离地检测与离地处理十分重要。理论上，严谨的离地处理需 要通过测得的关节输出扭矩来解算机器人实时受到的支持力，这将需要一定的推导计算。为 了项目进度，我们将该流程简化，直接用关节输出扭矩来判断机器人是否离地。图 12 为机 器人两次离地落地的关节扭矩输出，我们选取了离地阈值为 0.5Nm，经多次测试，该方式检 测离地较为可靠与高效。关于离地后的处理，我们将驱动轮的输出置零，并将位移和偏航角 两个状态变量置零，以使得机器人在落地后保持初始状态。

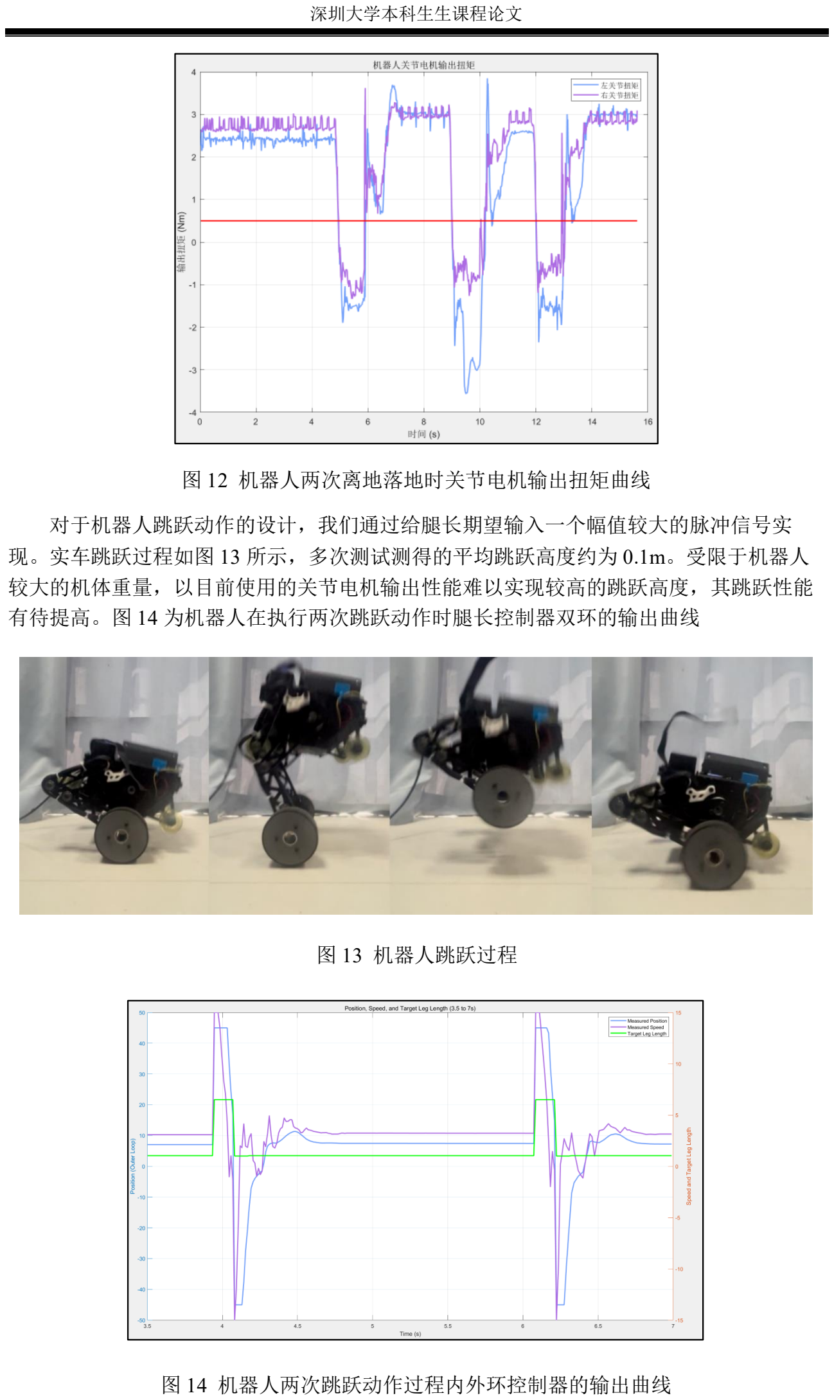
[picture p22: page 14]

图 12 机器人两次离地落地时关节电机输出扭矩曲线

对于机器人跳跃动作的设计，我们通过给腿长期望输入一个幅值较大的脉冲信号实 现。实车跳跃过程如图 13 所示，多次测试测得的平均跳跃高度约为 0.1m。受限于机器人 较大的机体重量，以目前使用的关节电机输出性能难以实现较高的跳跃高度，其跳跃性能 有待提高。图 14 为机器人在执行两次跳跃动作时腿长控制器双环的输出曲线

图 13 机器人跳跃过程

图 14 机器人两次跳跃动作过程内外环控制器的输出曲线

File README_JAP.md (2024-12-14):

# Wiibot

## 前書き
<div align="center">

</div>
<br>
<p align="center">このプロジェクトは、ロボット制御コースの課題設計の一環であり、バランスロボットの設計と制御を研究することを目的としています。本プロジェクトは以前のRP_Balanceプロジェクトに似ていますが、異なる脚構成を採用し、研究と分析をサポートするためにテストデータを保持しています。</p>
<p align="center">ロボットの機械部分はRobotPilots研究所のZJHが担当し、視覚認識部分はZZが担当しました。</p>

## 電子制御ハードウェア一覧
| 名称 | 技術仕様 | 機能 | 数量 |
|---|---|---|---|
| Robomaster 開発ボード C型 | 入力電圧: 8-28 V<br>IMU+Eコンパス: 1個<br>CANバス: CAN1: 2ポート; CAN2: 2ポート<br>UARTポート: 2個<br>SPIポート: 1個 | 高性能チップを搭載し、制御周波数は最大1000Hz。モーター通信、リモート信号受信、視覚モジュール通信を担当。 | 1 |
| Mike MC6mini リモートコントローラー受信機 | チャンネル数: 6<br>周波数範囲: 2401-2478 MHz<br>制御範囲: >800 m | ロボットの移動、回転、ジャンプなどの動作指令を送信。 | 1 |
| Lingkong MG6012E-i8v3 サーボモーター | 定格電圧: 48 V<br>無負荷回転速度: 310 rpm<br>定格トルク: 6 Nm<br>ピークトルク: 16 Nm | 脚の長さとロボット本体のロール角を制御。 | 2 |
| Robomaster GM6020 モーター | 定格電圧: 24 V<br>無負荷回転速度: 320 rpm<br>定格トルク: 1.2 Nm<br>ピークトルク: 1.4 Nm | ロボットの車輪を駆動し、移動、回転、バランスを実現。 | 2 |
| DJI M600 TB47S インテリジェントバッテリー | 容量: 4500 mAh<br>電圧: 22.2 V | ロボットの全体の電力供給を提供。 | 1 |
| DC-DC 調整可能電源モジュール | 入力電圧: 7-32 V<br>出力電圧: 0-28 V<br>定電流範囲: 0.2-1.2 A | 視覚認識用NUCに安定した電圧と電流を供給。 | 1 |

## ファイル概要

| ファイル名 | 機能 | ファイルリンク |
|---|---|---|
| Code | MATLABコード（モデリング、制御器設計、ゲインフィッティング、データプロット）および実機コード（ハードウェアドライバ、通信プロトコル、モジュール制御、ロジック制御）。 | [CODE](https://github.com/WilliamGwok/Wiibot/tree/main/Code) |
| Display_Files | 機械、電気制御、視覚認識に関するレポートとプレゼンテーションファイル。 | [DISPLAY](https://github.com/WilliamGwok/Wiibot/tree/main/Disply_Files) |
| Mec | ロボットの機械設計図面を含む。 | [MEC](https://github.com/WilliamGwok/Wiibot/tree/main/Mec/balance) |
| Simulation | Webotsプラットフォーム用のロボットシミュレーションモデル*。 | [SIM](https://github.com/WilliamGwok/Wiibot/tree/main/Simulation/webots) |
| Test_Video | 実機テスト画像とビデオを含む。 | [VIDEO](https://github.com/WilliamGwok/Wiibot/tree/main/Test_Video) |

*STLファイルをWebotsプラットフォームにインポートするのは複雑で、簡略化されたモデルでもシミュレーションが正常に動作しない場合がありました。最終的にバランス維持の機能のみが検証されました。

## 実機テスト

全体の制御器の性能がテストおよび分析されました。脚の長さ制御器とロール角制御器のテストを除き、その他のテストは固定脚の長さの条件下で実施されました。対応するゲイン行列Kは以下の通りです。全てのデータはJ-Scopeで測定され、MATLABでプロットされています：

$$
K={\left[\begin{array}{l l l l l l}{-3.693}&{-3.287}&{-8.559}&{-0.591}&{3.693}&{0.369; }\\ {-3.693}&{-3.287}&{-8.559}&{-0.591}&{-3.693}&{-0.369}\end{array}\right]}
$$

### バランスロボットの変位、ヨー角の静的応答、およびピッチ角の変化

静止状態で、振幅0.4のステップ信号を入力し、ロボットの変位応答とピッチ角の変化をテストしました。結果は図1の通りです。

<div align="center">

</div>
<br>
<p align="center">図1 変位ステップ応答およびピッチ角の変化</p>

測定された変位応答の特性は以下の通りです：

- ピーク時間 $T_{P}$：1.731s
- オーバーシュート $\upsigma\%$：17%
- 調整時間 $T_{S}$（誤差5%以内）：2.542s

変位応答の過程で、最大ピッチ角は0.219rad（約12.549度）でした。

静止状態で、振幅1.579（約90度）のヨーステップ信号を入力し、ヨー応答とピッチ角の変化をテストしました。結果は図2の通りです。

<div align="center">

</div>
<br>
<p align="center">図2 ヨーステップ応答およびピッチ角の変化</p>

ヨー応答の特性は以下の通りです：

- ピーク時間 $T_{P}$：0.477s

- オーバーシュート $\upsigma\%$：1.6%

- 調整時間 $T_{S}$（誤差5%以内）：0.385s

ヨー角の軌道追従中、ピッチ角は0.104rad以内で小さな振動を発生しました。

### 脚長およびロボット本体のロール角応答

脚長制御にはデュアルループPID制御器を使用しました。振幅0.3のステップ信号を入力した場合、外部位置ループと内部速度ループの応答は図3のようになりました。

制御器のパラメータ：

$$
\begin{array}{l}{{K p=100,\qquad K i=0.5,\qquad I n t e r g r a l_{m a x}=10,\qquad O u t_{m a x}=30;}}\\ {{\mathrm{}}}\\ {{\mathrm{}\kappa p=0.4,\qquad K i=0.05,\qquad I n t e r g r a l_{m a x}=5,\qquad O u t_{m a x}=8;}}\end{array}
$$

<div align="center">

</div>
<br>
<p align="center">図3 脚長デュアルループ制御器の応答</p>

最大脚長ステップ信号を入力した場合、応答は図4のようになりました。

<div align="center">

</div>
<br>
<p align="center">図4 最大脚長ステップ応答</p>

測定された脚長応答の特性は以下の通りです：

- ピーク時間 $T_{P}$：0.29s

- オーバーシュート $\upsigma\%$：6.07%

- 調整時間 $T_{S}$（誤差2%以内）：0.46s

ロール角応答は片側の坂を上る動作*で示され、そのロール角と左右の脚長の変化は図5の通りです。

<div align="center">

</div>
<br>
<p align="center">図5 坂を上る際のロール角と脚長の変化</p>

*坂を上るプロセスは2秒間続き、坂の長さは約0.8m、傾斜角は9°。

### 地面検知とジャンプ動作

関節トルクを監視することで地面検知を行いました。図6は2回の地面検知における関節トルクの出力曲線を示しています。地面検知の閾値は0.5Nmに設定され、テスト結果は高い信頼性を示しました。

<div align="center">

</div>
<br>
<p align="center">図6 地面検知におけるトルク曲線</p>

脚長に大幅なパルス信号を入力することでジャンプを実現しました。平均ジャンプ高さは約0.1mでした。モーター性能に制限されているため、ジャンプ高さには改良の余地があります。ジャンプ中の制御器出力は図7と図8の通りです。

<div align="center">

</div>
<br>
<p align="center">図7 ジャンププロセス</p>

<div align="center">

</div>
<br>
<p align="center">図8 ジャンプ動作の制御器出力曲線</p>

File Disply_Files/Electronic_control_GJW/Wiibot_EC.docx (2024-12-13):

1.系统建模

对于机器人的平衡，纵向以及转向运动，可以将模型简化为三维空间中的类一阶倒立摆模型，即忽略腿长的变化，转向运动由两个驱动轮差速运动控制。

1.1模型定义

称机器人机体质心到两个驱动轮转轴中心的连线为摆杆，得到如图1所示平衡车模型。

该模型的变量与参数定义如表1、表2所示。


图1 平衡车模型

表1 平衡车模型变量定义

符号 | 含义 | 正方向 | 单位
θ | 摆杆与竖直方向夹角 | 图示为正方向 | rad
φ | 摆杆偏航角 | 图示为正方向 | rad
x_i | 驱动轮位移 | X轴正方向 | m
x_b | 机体位移 | X轴正方向 | m
P_i | 驱动轮对摆杆力的竖直分量 | 箭头所示 | N
P_b | 摆杆受到的竖直方向力 | 箭头所示 | N
N_i | 驱动轮对摆杆力的水平分量 | 箭头所示 | N
N_b | 摆杆受到的水平方向力 | 箭头所示 | N
T_i | 驱动轮输出力矩 | 箭头所示 | N·m

表2 平衡车模型参数定义

符号 | 单位 | 含义
D | m | 车体转向直径
R | m | 驱动轮半径
L | m | 摆杆质心到驱动轮转轴中心的直线长度
m_w | kg | 驱动轮质量
m_b | kg | 摆杆质量
I_b | kg∙m^2 | 摆杆绕质心关于Z轴的转动惯量
I_w | kg∙m^2 | 驱动轮转子转动惯量
I_z | kg∙m^2 | 整车质心关于Y轴的转动惯量

1.2 经典力学分析

对驱动轮，有：

, m_w x_i =N_(fi) -N_i #(1)

, I_w (x_i)/R=T_i -N_(fi) R#(2)

对摆杆，有：

, m_b x_b =N_(fl) +N_(fr) #(3)

, m_b y_b =P_r +P_l -m_b g#(4)

, I_b _b =(P_r +P_l )Lsin_b -(N_r +N_l )Lcos_b -(T_r +T_l )#(5)

对整车，有：

, I_z ϕ=D/2(N_l -N_r )#(6)

其中：

, x_b =x+Lsin_b #(7)

, y_b =Lcos_b #(8)

1.3 状态空间模型

定义非线性模型：

x=f(x,T_l ,T_r )

利用MATLAB符号运算工具，联立式（1）到式（8），通过函数solve对方程组消去中间变量，最终得到非线性表达式（9），式（10），和式（11）

, 2m_w x+m_b (x-L(sin(_b )_b ^2 -_b cos(_b )))-(T_l)/R-(T_r)/R+(2I_w x)/(R^2)=0#(9)

T_l +T_r +I_b _b -Lsin(_b )(gm_b -Lm_b (cos(_b )_b ^2 +_b sin(_b )))-2Lm_w xcos(_b )

, +(LT_l cos(_b ))/R+(LT_r *cos(_b ))/R-(2I_w Lxcos(_b ))/(R^2)=0#(10)

, DT_l R=m_w ϕ_b D^2 R^2 +I_w ϕ_b D^2 +T_r DR+2I_z ϕ_b R^2 #(11)

定义状态向量x与控制向量u分别为：

x=[xx_b _b ϕϕ], u=[T_l T_r ]

根据式状态向量x与控制向量u，求非线性模型在平衡点处的雅可比矩阵并对其线性化，即将 =0 ，则 sin=,cos=1 代入式（9）到（11）后，求：

A=(∂f)/(∂x)(x,u), B=(∂f)/(∂u)(x,u)

其中，x、u是系统平衡点，即方程 f(x, u)=0 的解：

x=[x_b 000ϕ_b 0], u=[00]

最终求得的状态方程为：

, x=[0, 1, 0, 0, 0, 00, 0, A_1 , A_2 , 0, 00, 0, 0, 1, 0, 00, 0, A_3 , A_4 , 0, 00, 0, 0, 0, 0, 10, 0, 0, 0, 0, 0]x+[0, 0B_1 , B_2 0, 0B_3 , B_4 0, 0B_5 , B_6 ]u#(12)

由于表达式略为复杂，此处用符号代替，具体内容可通过运行MATLAB代码在工作空间中查看。

所有变量均可通过平衡车上各个传感器（如驱动轮编码器，IMU模块等）直接测量或通过数据融合解算得到，故可得系统输出 y=I_6 x ，其中 I_6 为单位阵。

代入平衡车实车模型参数后可以得到该状态空间模型的状态矩阵A和控制矩阵B，在MATLAB中使用rank函数求得其可控矩阵满秩，系统可控。系统输出矩阵C为单位矩阵，系统可观。

1.4 仿真验证

将Solidwork中搭建的模型分模块导入到仿真软件Webots中，通过对关节电机设置其允许位移为0，得到一个定腿长的平衡车模型。

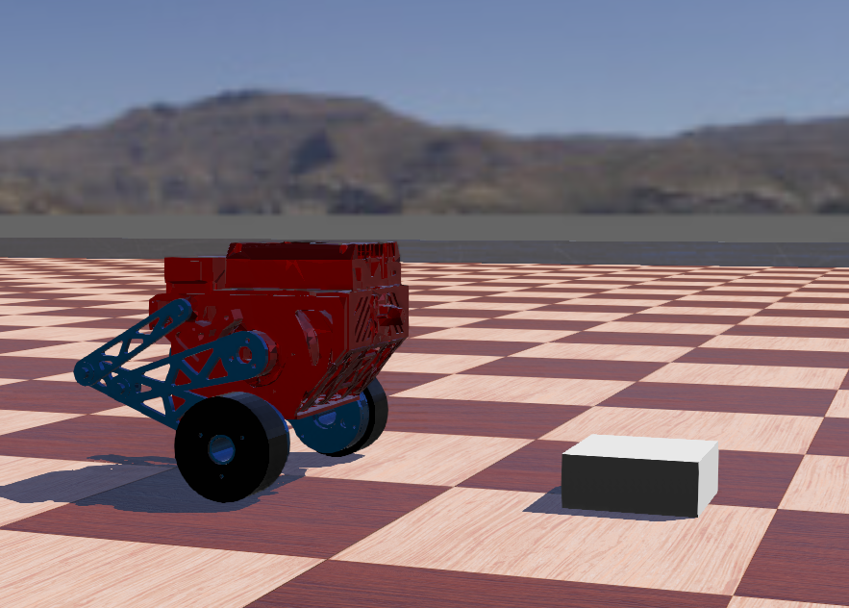
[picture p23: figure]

图2 仿真环境中的整车模型

通过使用MATLAB中的lqr函数计算得到反馈增益矩阵K。因为在仿真中主要目的是验证模型建立是否正确，用于计算K矩阵的Q和R权矩阵的数值选取只关注机器人俯仰角的稳定。经检验，得到模型正确。

2 控制器设计

基于本项目的平衡车构型，除了机器人的平移、转向和保持平衡的控制外，还需要控制平衡车双腿的长度及其横滚角。

2.1 LQR控制器

基于上述求得的状态空间方程，通过一个LQR控制器可以较好地对机器人平移、旋转以及机体俯仰角进行控制。

设计控制律为系统状态的线性组合：

u=-Kx=-[K_11 , K_12 , K_13 , K_14 , K_15 , K_16 K_21 , K_22 , K_23 , K_24 , K_25 , K_26 ][xx_b _b ϕϕ]

通过线性二次型调节器计算反馈矩阵，定义代价函数为

J=∫_0^(∞) (x^T Qx+u^T Ru)dt

其中：

- x 是系统状态向量；
- u 是控制输入向量；
- Q 是对状态变量的加权矩阵，通常是半正定矩阵，反映了对状态偏离的惩罚；
- R 是对控制输入的加权矩阵，通常是正定矩阵，反映了对控制能量的惩罚。

最优控制律：

为了使代价函数 J 达到最小，控制输入 u 应满足以下关系：

u=-R^(-1) B^T Px

其中：

- P 是代数 Riccati 方程的解。

反馈增益矩阵：

通过上述控制律，反馈增益矩阵 K 可以表示为：

K=R^(-1) B^T P

代数 Riccati 方程:

矩阵 P 需要满足以下代数 Riccati 方程：

A^T P+PA-PBR^(-1) B^T P+Q=0

其中：

- A 和 B 是系统状态空间方程中的系统矩阵和输入矩阵。

为了可以控制平衡车的移动和转向，还需要实现对位移和偏航角两个状态变量的轨迹跟踪。在系统输入中加入参考输入，即状态期望：

u=-K(x-x_d )

其中 x_d 为：

x_d =[x_d 000ϕ_d 0]

x_d 为期望位移， ϕ_d 为期望偏航角，两者均由其期望一阶微分量对时间积分得到。

2.2 双环PID控制器

基于该项目平衡车的四连杆腿部构型，可以通过关节电机的输出来调整机器人的腿部长度；同时，为了让机器人在进行视觉识别时机体保持横滚角水平，还需要根据机器人实时的横滚角值来调整两边腿的长度。

为了让机器人的腿长控制有更快的响应速度和鲁棒性，引入两个双环PID控制器分别对机器人的腿长和横滚角进行控制，最后并行输出到电机控制电流值。

腿长的控制框图如图3所示：

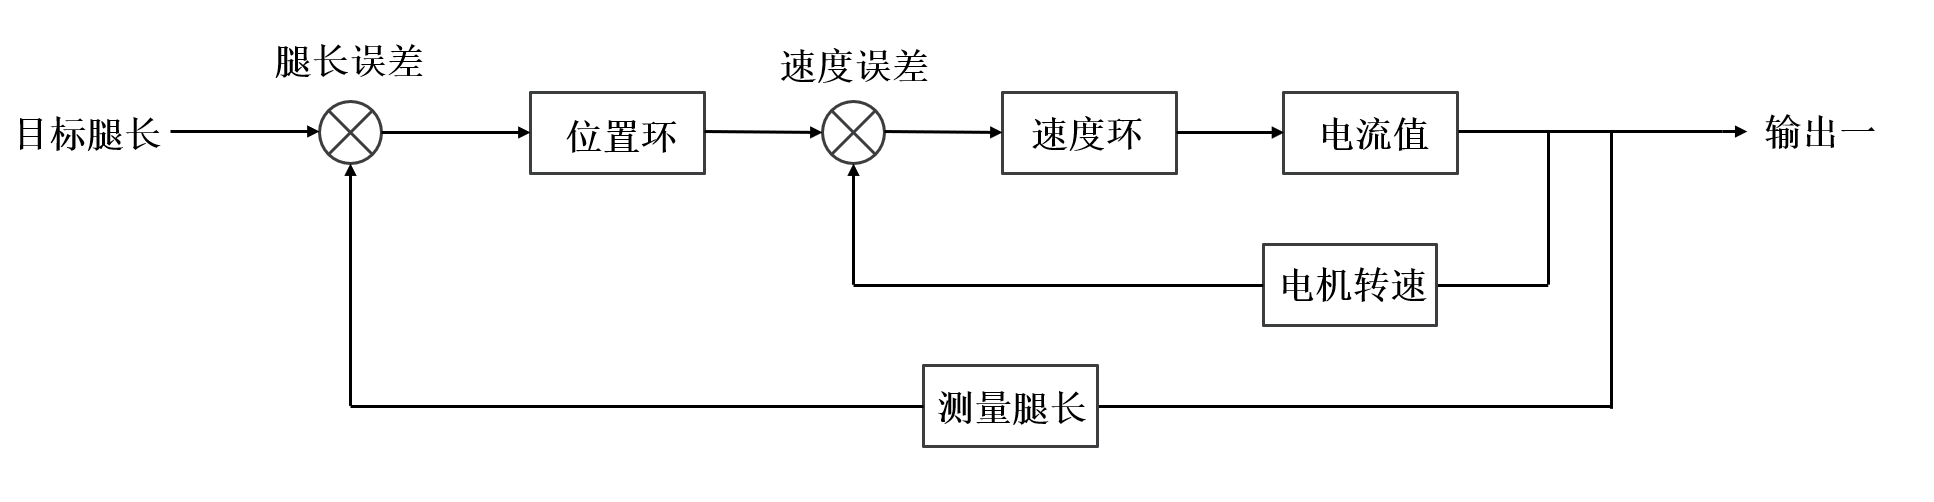
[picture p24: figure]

图3 机器人腿长双环PID控制框图

横滚角的控制框图如图4所示：

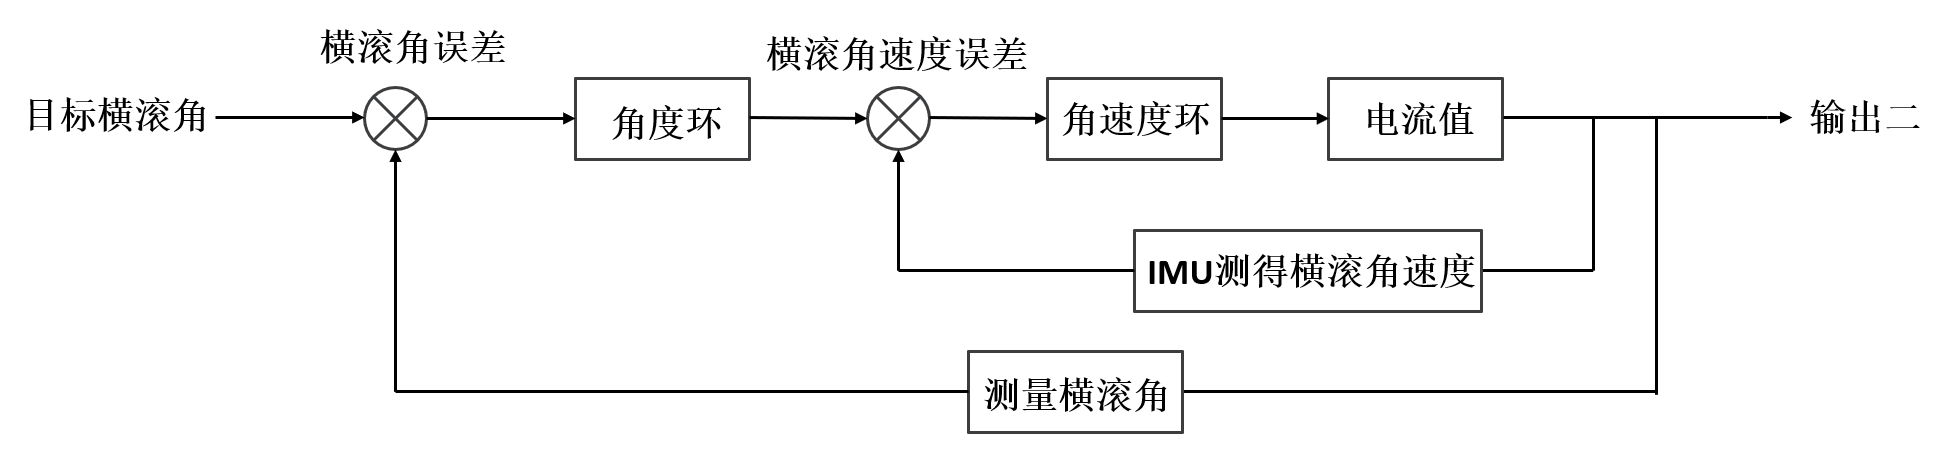
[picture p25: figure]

图4 机器人横滚角双环PID控制框图

最终发送的电机电流值为两个控制器的输出之和。

2.3 增益矩阵K的参数拟合

在建模阶段，我们将倒立摆的杆长假设为定值，但实际上，该值会随着机器人腿长的变化而改变，其对应的模型也会有差异。由于求得解析解较为困难，我们将机器人腿长作为拟合的自变量，对增益矩阵K进行四阶多项式拟合。

由于实车环境下我们无法直接测量机器人实时腿长，需要由一些角度关系推算得到。将模型简化至如图5所示。

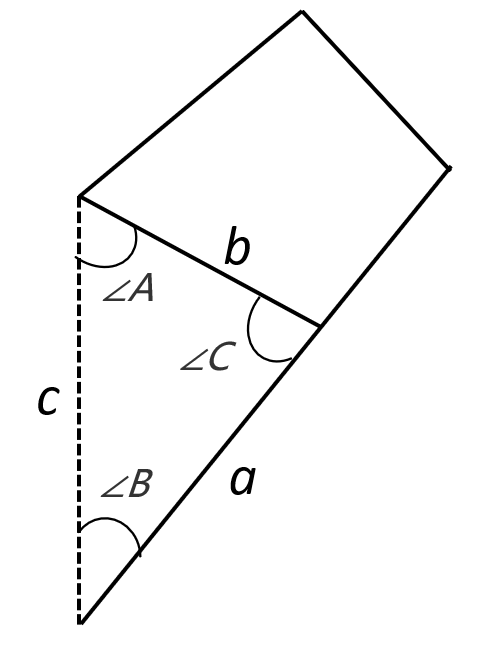
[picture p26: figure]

图5 腿部四连杆结构简化模型

其中，三角形边a、边b可以通过在机械图纸中测量得到，角A可以由电机编码器求得，边c则是期望求得的机器人腿长。由余弦定理得式（13）：

, a^2 -b^2 -c^2 +2bccos(A)=0#(13)

通过MATLAB的solve函数求解（排除负数解）得式（14）：

, c=bcos(A)+√(a^2 +b^2 cos^2 (A)-b^2)#(14)

经测量，实车边 b=0.11291m ，边 a=0.11461m ，将数据代入并由0至90度遍历角A可以得到角A与腿长的关系曲线如图6所示。


图6 机器人腿长与角度A的关系曲线

在MATLAB中遍历腿长，计算不同腿长值下的增益矩阵K，并对K矩阵每个元素进行关于角度A的多项式拟合，求得拟合系数并存到EXCEL表格中，以便将它们添加进实车代码中进行增益矩阵的实时计算。

拟合公式如式（15）：

y=a_4 x^4 +a_3 x^3 +a_2 x^2 +a_1 x+a_0

其中y对应K矩阵的各个元素，x为测得角度A的值。

最终的拟合效果如图7所示，蓝色曲线为各个角度A值下的实际K矩阵值，紫色曲线为拟合值。

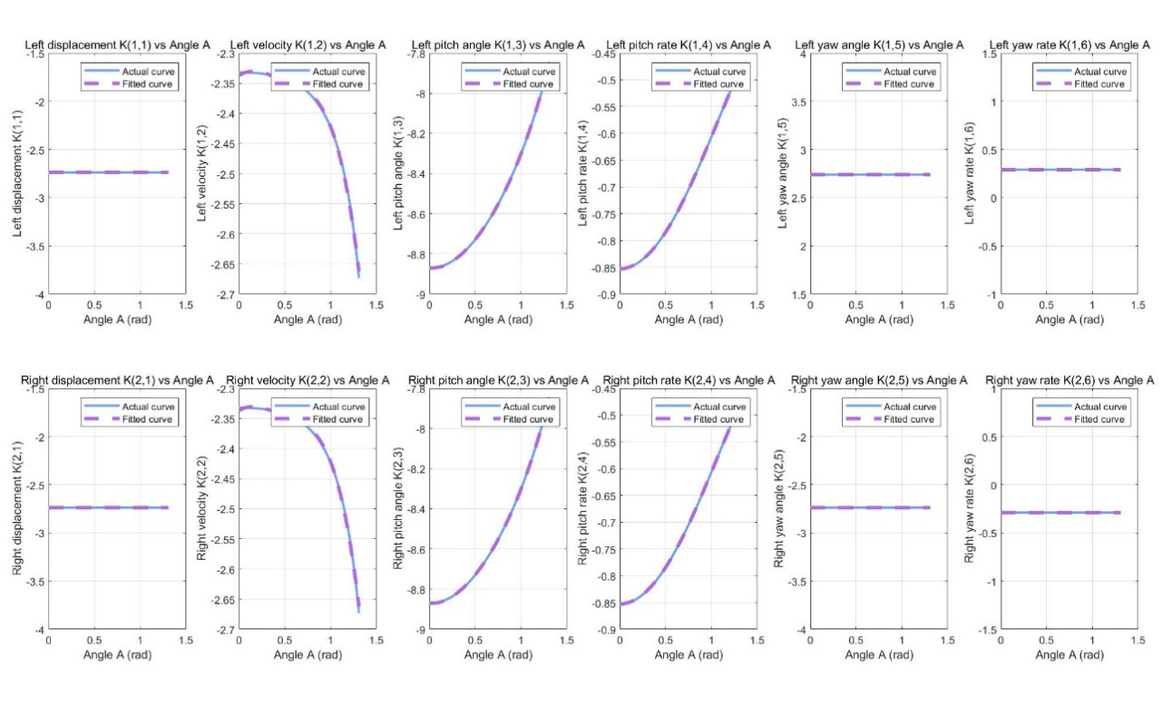
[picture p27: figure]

图7 增益矩阵K的实际曲线与拟合曲线对比

通过对比，可知拟合效果满足实车控制需求。

3. 实车硬件选型及代码框架介绍

基于项目需求及材料储备，本次选取的电控硬件型号如表3所示。

表3 平衡车实车主要电控硬件表

名称 | 部分技术参数 | 功能 | 数量
Robomaster开发板C型 | 输入电压：8-28 V IMU+E-compass：1个 CAN总线接口：CAN1：2个；CAN2：2个 UART接口：2个 SPI接口：1个 | 搭载的芯片提供足够高的运算能力，让机器人控制频率保持1000Hz。电机通讯、遥控器信息接收以及视觉电脑通讯 | 1
迈克mc6cmini遥控器航模接收器接收机 | 通道数量：6 频率范围：2401-2478 Mhz 控制范围：>800 m | 发送摇杆值，发送机器人平移、旋转、跳跃等指令 | 1
瓴控MG6012E-i8v3伺服电机 | 额定电压：48 V 空载转速：310 rpm 额定扭矩：6 Nm 峰值扭矩：16 Nm | 机器人关节电机，控制机器人的腿长以及机体横滚角 | 2
Robomater GM6020电机 | 额定电压：24 V 空载转速：320 rpm 额定扭矩：1.2 Nm 峰值扭矩：1.4 Nm | 机器人驱动轮电机，执行平移、旋转、维持平衡等动作 | 2
经纬M600系列TB47S智能飞行电池 | 容量: 4500 mAh 电压: 22.2 V | 整套机器人电控系统的供电 | 1
DC-DC可调电源模块 | 输入电压：7-32 V 输出电压：0.8-28 V 恒流范围：0.2-12 A | 为视觉电脑提供适配的工作电压及电流 | 1

4. 实车测试结果与数据分析

对整车多个控制器的控制效果进行分析，除了腿长控制器和横滚角控制器的测试，所有数据测量均在固定腿长的实车状态下测得，对应的增益矩阵K如下所示。数据均在J-Scope中测得，在MATLAB中绘制。

, K=[-3.693, -3.287, -8.559, -0.591, 3.693, 0.369-3.693, -3.287, -8.559, -0.591, -3.693, -0.369]

4.1 平衡车位移、偏航角静态响应及俯仰角变化

在静止状态下，给机器人位移期望输入幅值为 0.4 的阶跃信号，其位移响应及俯仰角变化如图8所示。


图8 机器人位移阶跃响应及其过程俯仰角变化

经测量，位移响应的峰值时间 T_P 为：

T_P =1.731s

超调量σ%为：

%=(A_(max) -A_(steady))/(A_(steady))×100%=(0.468-0.400)/0.4×100%=17%

调节时间 T_S 为（5%误差下）：

T_S =2.542s

在位移状态量的轨迹跟踪过程中，测得机器人机体最大俯仰角为 0.219 rad ，即约12.549度。

在静止状态下，给机器人偏航角期望输入幅值为 1.579 （约90度）的阶跃信号，其偏航角响应及俯仰角变化如图9所示。


图9 机器人偏航角阶跃响应及其过程俯仰角变化

经测量，位移响应的峰值时间 T_P 为：

T_P =0.477s

超调量σ%为：

%=(A_(max) -A_(steady))/(A_(steady))×100%=(1.585-1.560)/1.560×100%=1.6%

调节时间 T_S 为（5%误差下）：

T_S =0.385s

在偏航角状态量的轨迹跟踪过程中，测得机器人机体俯仰角在转动过程中会在 0.104 rad 内产生小幅度震荡。

综上，机器人位移响应速度较慢，考虑到测量过程中没有加入机器人速度状态的轨迹跟踪，且响应过程中机体倾角较小，实际响应效果可以满足项目需求。偏航角的响应十分迅速，且超调量小，对机体的俯仰角影响十分有限，也能满足项目需求。

4.2 平衡车腿长及机体横滚角响应

对于机器人腿长的控制，我们采用了双环PID控制器。对腿长目标值输入幅值为0.3的阶跃信号。其位置外环及速度内环的响应曲线如图10所示。

其中，该PID控制器的内外环参数如下所示：

位置环外环：Kp=100, Ki=0.5, Intergral_(max) =10, Out_(max) =30;

速度环外环：Kp=0.4, Ki=0.05, Intergral_(max) =5, Out_(max) =8;

基于关节电机的扭矩参数，额定扭矩为 6N∙m ，峰值扭矩为 16N∙m ，设置常态下速度环的最大速出为8，即 8N∙m 。


图10 机器人腿长双环控制器的内外环响应曲线

由图10可以看到，速度响应在初始阶段有一段锯齿波形，这是由于机械的腿部涉及有一些干涉导致的。再次输入阶跃信号，其幅值为机器人的最高腿长，其响应曲线如图11所示。


图11 机器人腿长最大阶跃响应曲线

经测量，腿长响应的峰值时间 T_P 为：

T_P =0.29s

超调量σ%为：

%=(A_(max) -A_(steady))/(A_(steady))×100%=(0.366-0.350)/0.350×100%=6.07%

调节时间 T_S 为（2%误差下）：

T_S =0.46s

关于机器人横滚角的响应，我们通过让机器人完成单侧上坡的动作来体现。其上坡过程中的横滚角变化曲线及左右腿腿长变化曲线如图12所示。


图12 机器人单侧上坡时测得的机体横滚角和两腿长度

由图12可以得到，在单侧上坡过程中，通过横滚角PID控制器控制双边腿长发生改变，来使得机体始终保持横滚角为0。由测得数据可知，该过程中机器人横滚角的变化幅值为0到0.07 rad，该横滚角响应性能满足项目需求。

4.3 离地检测与跳跃动作

在机器人跳跃过程中，机器人整体会完全离开地面，此时其模型与在地面时有差异，这将会导致系统发散。故高效的离地检测与离地处理十分重要。理论上，严谨的离地处理需要通过测得的关节输出扭矩来解算机器人实时受到的支持力，这将需要一定的推导计算。为了项目进度，我们将该流程简化，直接用关节输出扭矩来判断机器人是否离地。图13为机器人两次离地落地的关节扭矩输出，我们选取了离地阈值为0.5Nm，经多次测试，该方式检测离地较为可靠与高效。关于离地后的处理，我们将驱动轮的输出置零，并将位移和偏航角两个状态变量置零，以使得机器人在落地后保持初始状态。


图13 机器人两次离地落地时关节电机输出扭矩曲线

对于机器人跳跃动作的设计，我们通过给腿长期望输入一个幅值较大的脉冲信号实现。实车跳跃过程如图14所示，多次测试测得的平均跳跃高度约为0.1m。受限于机器人较大的机体重量，以目前使用的关节电机输出性能难以实现较高的跳跃高度，其跳跃性能有待提高。图15为机器人在执行两次跳跃动作时腿长控制器双环的输出曲线


图14 机器人跳跃过程


图15 机器人两次跳跃动作过程内外环控制器的输出曲线

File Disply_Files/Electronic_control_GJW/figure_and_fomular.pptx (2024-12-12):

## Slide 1

m_() x_i =N_(fi) −N_i
I_() (x_i)/R=T_i −N_(fi) R
m_b x_b =N_(fl) +N_(fr)
m_b y_b =P_r +P_l −m_b g
I_b _b =(P_r +P_l )Lsin_b −(N_r +N_l )Lcos_b −(T_r +T_l )
I_z φ=D/2(N_l −N_r )
x_b =x+Lsin_b
y_b =Lcos_b
x=f(x,T_l ,T_r )

P_l

y

P_b

N_l

N_b

T_l

N_(fl)

θ

m_b g

φ

x

O

L

1/2D

P_r

N_r

N_(fr)

T_r

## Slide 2

腿长误差

速度误差

目标腿长

位置环

速度环

电流值

输出一

电机转速

测量腿长

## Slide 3

横滚角误差

横滚角速度误差

目标横滚角

角度环

角速度环

电流值

输出二

IMU测得横滚角速度

测量横滚角

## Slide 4

b

∠A

∠C

a

c

∠B

T_S

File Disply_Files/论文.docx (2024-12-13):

深圳大学本科生课程论文

题目 基于CNN和PCA的人脸识别 成绩

专业 课程名称、代码

年级 2022 姓名

学号 时间2024 年10月9日

任课教师

深圳大学本科生课程论文学术诚信承诺书

本人在此声明所提交的课程论文基于CNN和PCA的人脸识别是本人独立完成的，具有原创性，并且未抄袭、剽窃他人成果或侵犯他人的知识产权。本声明书详细阐述以下内容：

1.本人郑重声明，课程论文的所有内容和观点均源自本人的研究和分析，未从其他来源直接复制或翻译。

2.对于其他作者或研究人员的观点、数据、图片、图表等引用和参考，本人已按照学校规定的引用标准进行准确的引用和注明，并在文中明确标明了引用部分。

3.本人保证，课程论文中使用的所有文献、资料和其他来源均已在参考文献部分列出，且准确无误地注明了相关信息，包括作者、出版年份、出版社或期刊名称等。未使用生成式人工智能文本生成工具。

4.本人明确知晓学术不端行为的严重性，包括但不限于抄袭、剽窃、造假、篡改数据等。本人承诺，在课程论文的整个研究和撰写过程中，坚守学术道德原则，维护学术诚信。

我郑重承诺以上内容的真实性，并愿意为我所提交的课程论文的原创性负全部责任。

论文作者签名： 日期： 年 月 日

# 图 目 录

基于CNN和PCA的人脸识别

# 【摘要】：随着深度学习技术的快速发展，人脸识别技术在安全、监控、金融等多个领域得到了广泛应用。本文针对人脸识别中的关键问题，研究了基于卷积神经网络（CNN）和主成分分析法（PCA）的混合模型。首先，本文系统介绍了PCA和CNN的基本原理，分别应用这两种方法对人脸图像进行特征提取和分类。PCA通过降维技术减少了数据冗余，从而提高了计算效率，而CNN作为一种深度学习算法，通过多层卷积和池化操作，自动提取图像中的高维特征，展现出较高的识别精度。

此外，本文结合了K近邻算法（KNN）对PCA降维后的人脸特征进行分类，并设计了基于Matlab的图形用户界面（GUI），实现了人脸图像的预处理、分类和结果显示。实验部分采用了不同来源和场景下的人脸图像数据集，分别对PCA和CNN模型进行了训练和测试。结果表明，PCA结合KNN方法在人脸识别的特定场景中具有一定的优势，但在大规模数据处理上表现相对有限。而CNN在面对复杂的图像数据时，展现出更高的准确率和鲁棒性，特别是在多类别分类任务中表现突出。

通过对比分析，本文认为CNN由于其强大的特征提取能力和较少的参数依赖性，未来在人脸识别领域将有更广阔的应用前景。同时，结合PCA、KNN等传统算法的混合模型或将成为未来优化算法性能的一种重要研究方向。本文的研究为人脸识别技术的发展提供了理论支持，并在实践中为复杂场景下的身份识别问题提供了可行的解决方案。

【关键词】： 卷积神经网络（CNN），主成分分析（PCA），人脸识别，K近邻算法（KNN），深度学习，图像分类

# 1 绪论

## 1.1 研究背景及意义

人脸识别技术是一种利用人脸图像进行身份识别的技术，广泛应用于安全、监控、金融、医疗等领域。近年来，随着深度学习技术的发展，人脸识别技术取得了显著进展。卷积神经网络（CNN）因其在图像处理方面的强大能力，被广泛应用于人脸识别中。而K-近邻算法（KNN）作为一种简单但有效的分类算法，也在某些情况下展现出不错的性能。

## 1.2 国内外研究现状

KNN作为一种简单且有效的分类算法，在人脸识别中的应用较为普遍。研究者们通常将KNN与特征提取方法结合使用，如主成分分析（PCA）和线性判别分析（LDA），以提高识别精度。

例如，2016年孙志帅利用PCA和均匀采样去弥补Gabor小波变换造成维度增加的劣势[1]，既保证了Gabor小波变换识别率高的优势,又弥补了维度增加的劣势,达到了优势互补，并通过分析K最近邻法和支持向量机法各自优势，把两者相结合,利用K最近邻法初步定范围，用支持向量机最终识别分类,达到了优势互补,得到了 KNN-SVM分类算法。

2018年简彩仁等人利用主成分分析和核主成分分析对基于降维的人脸识别方法进行了研究[2]。实验结果表明降维可以有效地提高人脸识别准确率，而非线性降维方法更适合人脸图像数据的降维，并且降维后的数据可以明显提高识别效率。

2018年Mustafa Zuhaer Nayef Al-Dabagh等人提出了一种使用核判别分析（KDA）和支持向量机（SVM）结合K近邻（KNN）方法的人脸识别系统[3]。核判别分析用于从输入图像中提取特征，随后使用SVM和KNN根据提取的特征对人脸图像进行分类。

近年来，随着深度学习的发展，CNN在人脸识别中的应用逐渐成为主流。国内许多研究者致力于优化CNN架构，以提升其在复杂场景下的人脸识别性能。

例如，2019年李瑛将基于CNN的人脸识别技术应用在课堂考勤系统中[4]。研究利用K-Means聚类方法从大量标注数据中学习到人脸候选区域的若干典型值，并以此为基础优化Faster R-CNN人脸检测算法的RPN网络候选区域提取策略。且在已有基于CNN的人脸识别算法基础上，对其网络结构和参数进行有针对性的优化，得到一个该应用场景下的高效人脸识别模型。

2021年冯友兵等人针对人脸识别在实际应用中存在姿态变化、表情、遮挡等问题[5]，采用了基于facenet卷积神经网络的特征提取算法以及svm分类算法，在此基础上设计并实现了人脸识别系统。

2017年Musab Coşkun等人提出了一种基于CNN架构的人脸识别算法[6]。该算法的主要特征是在第一层和最后一层卷积层的输出上应用了批量归一化，从而使网络能够达到更高的准确率。在全连接层步骤中，使用Softmax分类器对人脸进行分类。

KNN和CNN在国内的人脸识别研究中各有侧重。KNN作为传统算法，在特定场景中与其他算法的结合显示出良好的效果，而CNN凭借深度学习的优势，逐渐成为人脸识别的主流方法。随着技术的发展，结合这两种方法的混合模型和更为复杂的深度学习架构将可能成为未来研究的重要方向。

# 2 PCA人脸识别实现

## 2.1 PCA介绍

主成分分析（Principal components analysis, PCA），顾名思义，其目的在于提取数据中的主要成分信息，因此，常用于对数据的提炼，例如：降维（使用最多的领域之一），异常值检测等，是数据分析中的一种重要方法。

## 2.2 PCA数学原理

我们希望投影后投影值尽可能分散，而这种分散程度，可以用数学上的方差表述，于是用两个字段的协方差表示其相关性。

当协方差为0时，表示两个字段完全独立。为了让协方差为0，我们选择第二个基时只能在与第一个基正交的方向上选择。因此最终选择的两个方向一定是正交的。协方差矩阵是一个对称矩阵，其对角线分别是各个字段的方差。

要进行优化，等价于将协方差矩阵对角化：即除对角线外的其他元素化为0，并且在对角线上将元素按大小从上到下排列，这样我们就达到了优化目的。

优化目标变成了寻找一个矩阵P，满足PCPT是一个对角矩阵，并且对角元素按从大到小依次排列，那么P的前K行就是要寻找的基，用P的前K行组成的矩阵乘以X就使得X从N维降到了K维并满足上述优化条件。

## 2.3 人脸识别和重建实验中的PCA算法

（1） 降维：所有图片构成的3维矩阵降维成2维，提升运算速度；
（2） 标准化：求所有图像各像素点的平均值，即平均脸；
（3） 中心化：原始数据减去平均量，中心化每一列为一张图；
（4） 由中心化向量得到协方差矩阵；
（5） 求解主成分：求解协方差矩阵的特征值与特征向量，对特征值和特征向量进行降序排序，取前d个特征向量，这d个特征向量组成的矩阵X即为选取的主成分
（6） 根据选取的d个特征向量构造特征脸W，W*X映射到脸空间，重构人脸

中心化后: 重构后的人脸：

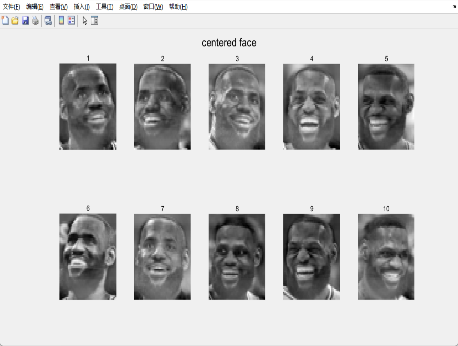
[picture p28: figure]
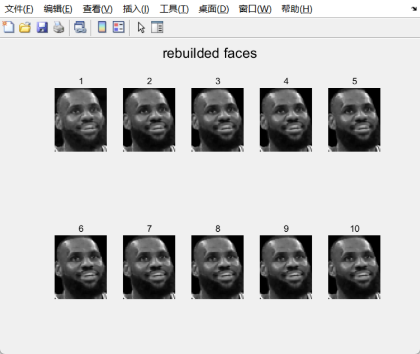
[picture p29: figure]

图 2-1中心脸 图 2-2重构脸

## 2.4 KNN

算法核心思想为：算法的核心思想为：给定一个训练数据集，对新的输入实例，在训练数据集中找到与该实例最邻近的K个实例，这K个实例的多数属于某个类，就把该输入实例分类到这个类中。

本实验对测试集的验证选择了KNN近邻类分类，算法步骤如下：

（1） 计算距离：本实验中距离定义为测试集与训练集映回脸空间后的矩阵相减的差值，差值越大距离越大，即越不可能为同一张脸
（2） 对距离进行升序排序
（3） 选取前k个距离，获取对应的标签（即对应的人脸），选取出现次数最多的label作为预测脸
（4） 预测label与测试脸label进行对比，最后用正确的人脸数除去测试集大小即为对应k值下的正确率。

# 3 CNN人脸识别

## 3.1 CNN与全连接网络的异同

（1） 结构

全连接网络的内部，层与层之间是全连接的，也就是说，第i层的任意一个神经元一定与第i+1层的任意一个神经元相连。全连接网络不具备对输入数据的空间结构处理能力。它将输入数据展平为一维向量，并丢失了原始数据的空间信息。

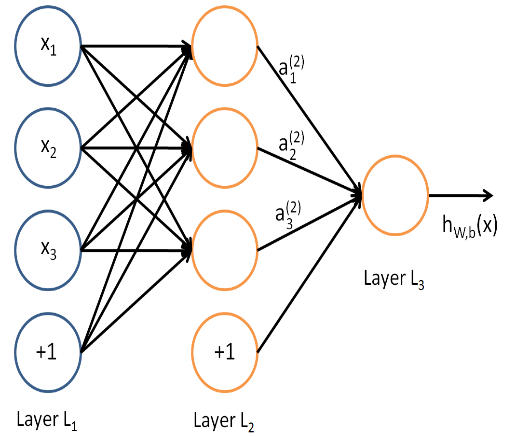
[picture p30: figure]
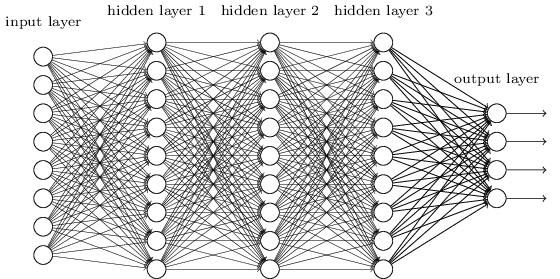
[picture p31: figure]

图 3-1 全连接网络结构

而CNN的隐藏层由卷积层、池化层和全连接层组成。卷积层用于提取输入数据中的局部特征，池化层用于降低特征图的尺寸并保留主要特征，全连接层用于将提取的特征映射到输出类别上。CNN的输入通常是张量，例如RGB图像，能够处理具有空间结构的数据。

图 3-2 CNN网络结构

（2）参数和数据效率：

使用卷积核在输入上滑动，可以共享权重来检测相同的特征模式，CNN通常具有较少的参数数量，尤其适用于处理大规模数据，例如图像。这也降低了计算复杂度，使得CNN更容易训练和部署。而全连接网络的参数数量较大

，尤其是在输入维度较高的情况下。CNN以从数据中提取出更少但更有代表性的特征，因此对于大规模数据集的训练效果较好。全连接网络通常需要更多的数据样本来获得好的泛化性能。否则，容易出现过拟合现象。并且，全连接网络由于每个神经元都有独立的权重，很难评估网络中每个神经元对结果的贡献。

（2） 算法上：

由于CNN多了卷积层和池化层，这两层的前向传播和后向传播的数学推导和具体实现上也不同。

## 3.2 推导CNN

### 3.2.1 . CNN前向传播

输入是张量,卷积层激活函数是ReLU;隐藏层前向传播到池化层只需对输入的矩阵进行缩小，池化标准一般是MAX或者Average；隐藏层前向传播到全连接层和DNN相同，但最后一层的输出层激活函数是softmax。

是卷积层： *表示卷积运算

是池化层： ，pool表示按池化大小和标准将输入张量缩小

是全连接层：

对于输出层第层:

### 3.2.2 CNN反向传播：

求出中间变量和的传递关系，来推导出上一层的梯度。

全连接层反向传播与DNN相同，主要探讨卷积层和池化层。

池化层的推导上一隐藏层的：

反向传播时，我们首先会把的所有子矩阵矩阵大小还原成池化之前的大小，然后如果是MAX，则把的所有子矩阵的各个池化局域的值放在之前做前向传播算法得到最大值的位置。如果是Average，则把的所有子矩阵的各个池化局域的值取平均后放在还原后的子矩阵位置。这个过程一般叫做upsample（上采样）。

（1）

卷积层的推导上一隐藏层的：

（2）

与DNN不同就是使用了卷积预算*并且卷积核被旋转了180度（先上下翻转一次再左右翻转一次）。

求出每层的梯度后可以求改成的的梯度，池化层没有就不用求，仅考虑卷积层。

由 ，得出 （3）

对于b,则有些特殊，因为是高维张量，而b只是一个向量，不能像DNN那样直接和相等。通常的做法是将的各个子矩阵的项分别求和，得到一个误差向量，即为b

的梯度： （4）

所以CNN反向传播使用梯度下降更新表示为

1）若为全连接层（则与DNN相同）： ，

2）若为卷积层： ，

## 3.3 CNN设计与技术实现

### 3.3.1 神经网络设计

本网络的设计目标是实现图像的分类，根据需求，我们使用了matlab的深度神经网络设计器来构建卷积神经网络。

具体设计如下：

（1） imageInputLayer：输入图像层，定义了输入图像的大小和通道数。
（2） convolution2dLayer：卷积层，执行二维卷积操作，用于提取特征。
（3） batchNormalizationLayer：批归一化层，标准化输入以加速训练和提高稳定性。
（4） reluLayer：激活层，应用ReLU（线性整流单元）激活函数，增加非线性。
（5） fullyConnectedLayer：全连接层，将前一层的所有神经元连接到该层的每个神 经元，通常用于分类。
（6） softmaxLayer：Softmax层，将输出转化为概率分布，适用于多类分类。
（7） classificationLayer：分类层，计算损失函数并评估分类性能。

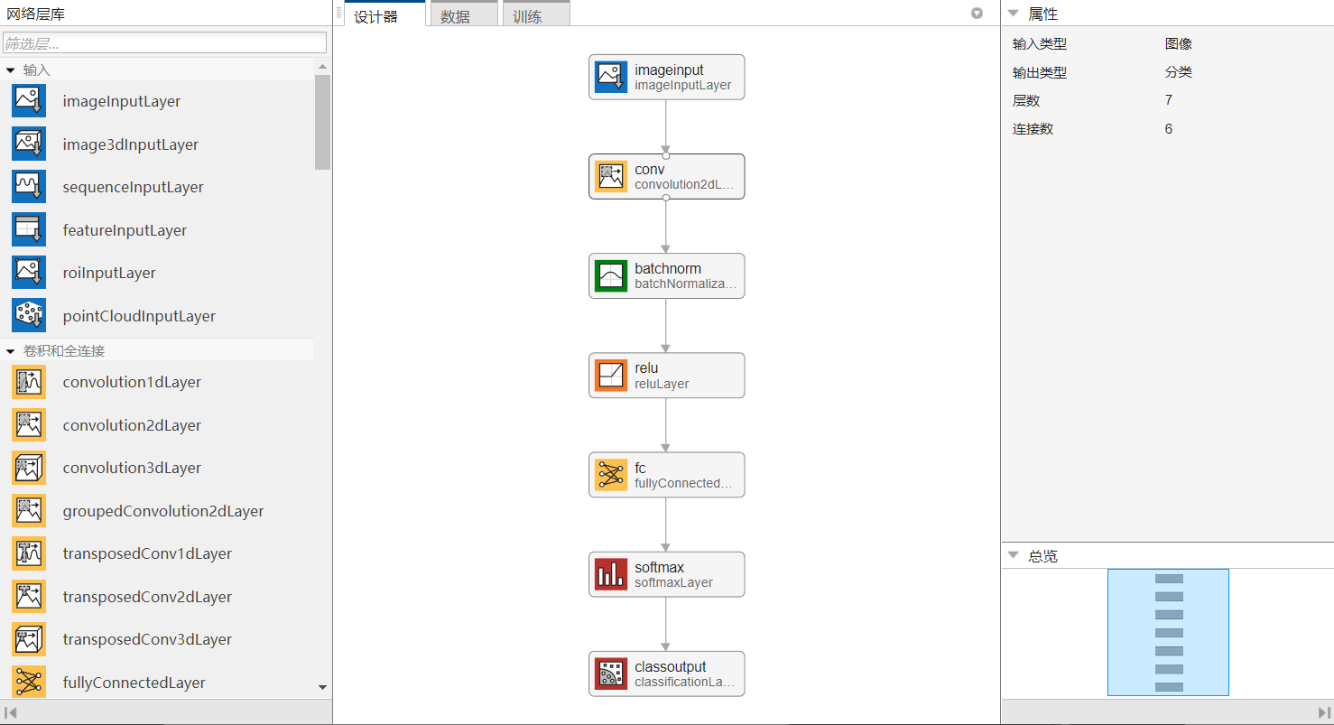
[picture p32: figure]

图 3-3

### 3.3.2 检验网络性能

设计好网络后，在APP中直接导入数据集，选取了30%的数据作为测试集，训练，并得到训练图及分类性能。经过30轮迭代后可以看到最终准确度达到100%，损失函数收敛，并且验证准确度达到100%，符合预期分类效果。

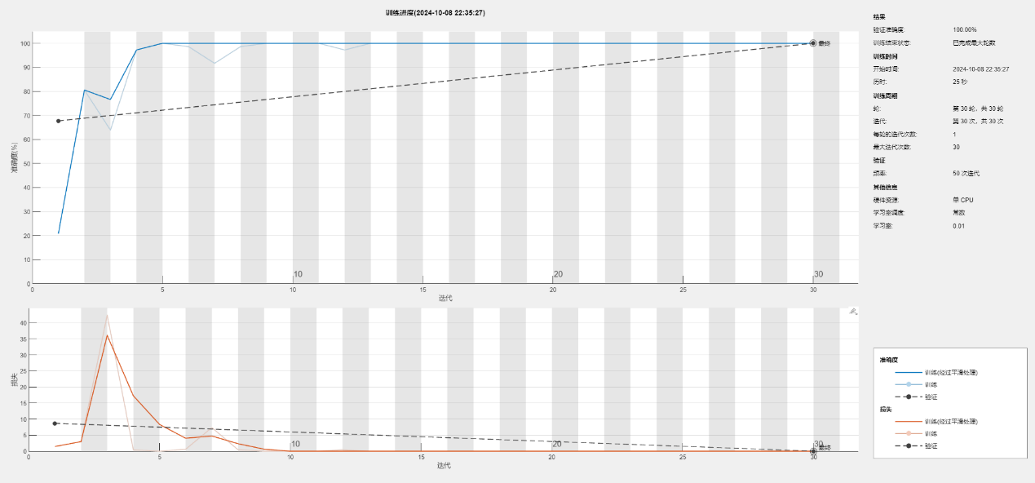
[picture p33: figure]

图 3-4 卷积神经网络训练结果

### 3.3.3 移植网络

为了后续GUI界面的开发，还需要将设计好的网络封装为函数，当调用时训练并返回训练好的网络和训练结果。每训练一轮就会调用progressFcn，方便后续在GUI界面上更新训练进程。函数代码如下。

function [net,traininfo] = cnn_train(app, train_folderPath)

imdsTrain = imageDatastore(train_folderPath, "IncludeSubfolders", true, "LabelSource", "foldernames");

% 分割数据集

[imdsTrain, imdsValidation] = splitEachLabel(imdsTrain, 0.7);

% 训练选项，包括 OutputFcn

opts = trainingOptions("sgdm",...

"ExecutionEnvironment","auto",...

"InitialLearnRate",0.01,...

"Shuffle","every-epoch",...

"Plots","none",...

"ValidationData",imdsValidation,...

"OutputFcn", @(info)progressFcn(app, info)); % 设置输出函数用于更新进度条

layers = [

imageInputLayer([128 100 3],"Name","imageinput")

convolution2dLayer([3 3],32,"Name","conv","Padding","same")

batchNormalizationLayer("Name","batchnorm")

reluLayer("Name","relu")

fullyConnectedLayer(3,"Name","fc")

softmaxLayer("Name","softmax")

classificationLayer("Name","classoutput")];

% 训练网络

[net, traininfo] = trainNetwork(imdsTrain, layers, opts);

end

### 3.3.4 分类部分

最终要实现对输入图像进行分类，调用classify(net,img)对输入图像进行分类。图像被输入到神经网络 net。网络从输入层开始，依次通过卷积层、激活层、批归一化层、全连接层等，进行前向传播计算。在最后一层（softmaxLayer），网络生成每个类别的预测概率。classify 函数根据这些概率输出预测的类别标签。

## 3.4 GUI设计

### 3.4.1 界面设计

GUI使用Matlab的App Designer进行设计，本GUI界面功能要求：

（1） 导入数据集
（2） 预览数据集
（3） KNN分类
（4） CNN网络训练
（5） CNN分类

根据要求设计的GUI界面如下。


图 3-5 GUI界面排版

### 3.4.2 交互设计

通过设计回调函数，实现组建之间的交互。

其中，点击左侧的“选择数据集按钮”来选择数据集存储的文件夹路径，并调用buildTree函数来更新下方显示文件夹结构的树，在树中选择对应的图片对数据集进行预览。以下是buildTree函数代码。

% 递归函数来构建树

function buildTree(app, parentNode, folderPath)

% 获取文件夹中的内容

items = dir(folderPath);

% 遍历每个项目

for i = 1:length(items)

if strcmp(items(i).name, '.') || strcmp(items(i).name, '..')

continue;

end

% 创建新的节点

fullPath = fullfile(folderPath, items(i).name);

if items(i).isdir

% 如果是文件夹，递归添加子节点

newNode = uitreenode(parentNode, 'Text', items(i).name, 'NodeData', fullPath);

buildTree(app, newNode, fullPath); % 递归调用

else

% 如果是文件，直接添加节点

if isImageFile(app,items(i).name)

newNode = uitreenode(parentNode, 'Text', items(i).name, 'NodeData', fullPath);

end

end

end

end

对于KNN界面，点击“选择测试图像按钮”选择要测试的分类图像，然后会在下方显示分类结果及所选的图像。效果如下图。


图 3-6 KNN分类效果

对于CNN界面，点击“训练”后开始训练，左侧显示训练进度条，训练完成后右侧则显示训练的结果的准确度和损失函数图像。点击“选择测试图像”选择要分类的图像后，在下方显示分类结果，右侧显示选择对应的图像。效果如下图。


图 3-7 CNN分类效果

# 4 测试实验与数据分析

## 4.1 实验设计

### 4.1.1 实验目的

检验本研究所设计KNN和CNN人脸识别架构对于实际人脸识别的识别效果。

### 4.1.2 实验方式

选定了詹姆斯，张元英和蜡笔小新作为识别对象， 从互联网或个人图库中收集每个对象的图片，确保每个对象至少包含30张不同场景的照片。对收集到的图片进行统一处理，包括调整大小、去噪声和标准化，使其适合输入到KNN和CNN模型中。使用KNN模型进行训练，并选择适当的K值。构建CNN模型，并进行训练。最后评估模型的性能，记录每种算法的识别准确率、错误率及处理时间。

## 4.2 实验过程

1) 在网络上收集不同来源的图片，确保多样性。将所有图片进行标签化，标记每张图片对应的对象。
2) 将所有图片调整为统一的尺寸。应用数据增强技术（如旋转、翻转、缩放等）来增加数据集的多样性。
3) 使用数据集进行模型训练。
4) 选取测试集测试模型的准确度

## 4.3 实验结果

导入数据集后，随机选取图像进行识别，KNN在导入图像时直接计算与数据集最匹配的标签，识别效果如下图。


图 4-1 蜡笔小新KNN识别结果 图 4-2 张元英KNN识别结果

CNN在导入数据后，点击训练等待训练结束，选择测试图像得出最匹配的分类标签，识别效果如下。


图 4-3 蜡笔小新CNN识别结果 图 4-4詹姆斯CNN识别结果

经过测试和统计，PCA和CNN的识别准确度都在90%以上，符合预期标准。

# 5 总结和展望

## 5.1 总结

本文研究了基于卷积神经网络（CNN）和主成分分析法（PCA）的人脸识别技术，系统分析了两种算法在人脸识别中的应用效果。通过对PCA和K近邻算法（KNN）的结合，本文实现了对人脸特征的降维与分类，在特定数据集上取得了较好的分类准确率。然而，随着数据量的增加，PCA的局限性逐渐显现，特别是在处理大规模图像数据时，其特征提取能力不足。相较之下，CNN通过自动提取图像的高维特征，展现出更强的识别能力和更高的精度，尤其适用于处理复杂场景下的人脸识别任务。通过实验验证，CNN在人脸识别的表现优于传统的PCA-KNN组合，并在数据处理的效率和准确性方面具备显著优势。

本研究还设计了基于Matlab的图形用户界面（GUI），使用户能够便捷地进行人脸数据的预处理、分类和结果展示。

## 5.2 展望

随着人工智能技术的不断进步，人脸识别领域仍有广阔的发展前景。未来的研究可以在以下几个方面展开：

（1） 优化CNN结构：虽然CNN在人脸识别中的表现已经非常优秀，但其在训练过程中对硬件资源的要求较高。未来可以进一步研究轻量化网络结构，如MobileNet、ShuffleNet等，以提升模型的计算效率，降低训练成本。
（2） 混合模型的探索：尽管CNN已经在图像识别领域占据主流，但传统的PCA、LDA等算法在特定场景下依然具有优势。未来可以探索更多混合模型，将传统方法与深度学习技术相结合，以提高模型的鲁棒性和适应性。
（3） 数据增强与迁移学习：为提升模型的泛化能力，未来可以结合数据增强技术和迁移学习，通过扩展训练数据集的多样性来增强模型在不同应用场景下的表现。
（4） 应用领域的扩展：人脸识别技术已广泛应用于安防、考勤等领域，但随着深度学习和计算机视觉技术的发展，未来可以探索更多垂直行业的应用场景，如医疗诊断、情感识别等，进一步拓展人脸识别的应用边界。

通过不断优化模型结构、融合更多先进技术，人脸识别技术将在未来的智能社会中扮演更加重要的角色，并为更多领域提供创新性的解决方案。

# 参考文献

[1] 孙志帅.基于Gabor-PCA和KNN-SVM的人脸识别算法[D].null,2016.
[2] 简彩仁,庄凌宇,林智鹏.基于降维的人脸识别方法研究与应用[J].信息技术与网络安全,2018,37(12):75-78.DOI:10.19358/j.issn.2096-5133.2018.12.017.
[3] Al-Dabagh M Z N, Alhabib M H M, Al-Mukhtar F H. Face recognition system based on kernel discriminant analysis, k-nearest neighbor and support vector machine[J]. International Journal of Research and Engineering, 2018, 5(3): 335-338.
[4] 李瑛.基于CNN的人脸识别技术在课堂考勤系统中的应用[D].null,2019
[5] 冯友兵，陆轶秋，仲伟波.基于CNN 和SVM 的人脸识别系统的设计与实现∗[J].计算机与数字工程,2021,第49卷(2): 378-382，420
[6] Coşkun M, Uçar A, Yildirim Ö, et al. Face recognition based on convolutional neural network[C]//2017 international conference on modern electrical and energy systems (MEES). IEEE, 2017: 376-379.

【Abstract】With the rapid development of deep learning technologies, facial recognition has been widely applied in various fields such as security, surveillance, and finance. This paper addresses key issues in facial recognition by studying a hybrid model based on Convolutional Neural Networks (CNN) and Principal Component Analysis (PCA). First, the basic principles of PCA and CNN are systematically introduced, and these two methods are respectively applied to extract and classify features from facial images. PCA reduces data redundancy through dimensionality reduction, thus improving computational efficiency, while CNN, as a deep learning algorithm, automatically extracts high-dimensional features from images through multiple layers of convolution and pooling, showing high recognition accuracy.

Furthermore, the paper combines the K-Nearest Neighbors (KNN) algorithm to classify facial features after PCA dimensionality reduction and designs a Graphical User Interface (GUI) based on MATLAB to implement facial image preprocessing, classification, and result display. The experiments utilized facial image datasets from various sources and scenes to train and test the PCA and CNN models. The results indicate that the PCA combined with KNN method has certain advantages in specific scenarios of facial recognition, but its performance is relatively limited in large-scale data processing. On the other hand, CNN demonstrated higher accuracy and robustness when handling complex image data, particularly excelling in multi-class classification tasks.

Through comparative analysis, this study concludes that CNN, due to its powerful feature extraction capabilities and reduced reliance on parameters, has broader future applications in facial recognition. Additionally, the combination of traditional algorithms such as PCA and KNN with deep learning techniques may become an important research direction for optimizing algorithm performance in the future. This research provides theoretical support for the development of facial recognition technology and offers practical solutions for identity recognition challenges in complex scenarios.

【Keywords】Convolutional Neural Network (CNN); Principal Component Analysis (PCA); facial recognition; K-Nearest Neighbors (KNN); deep learning, image classification

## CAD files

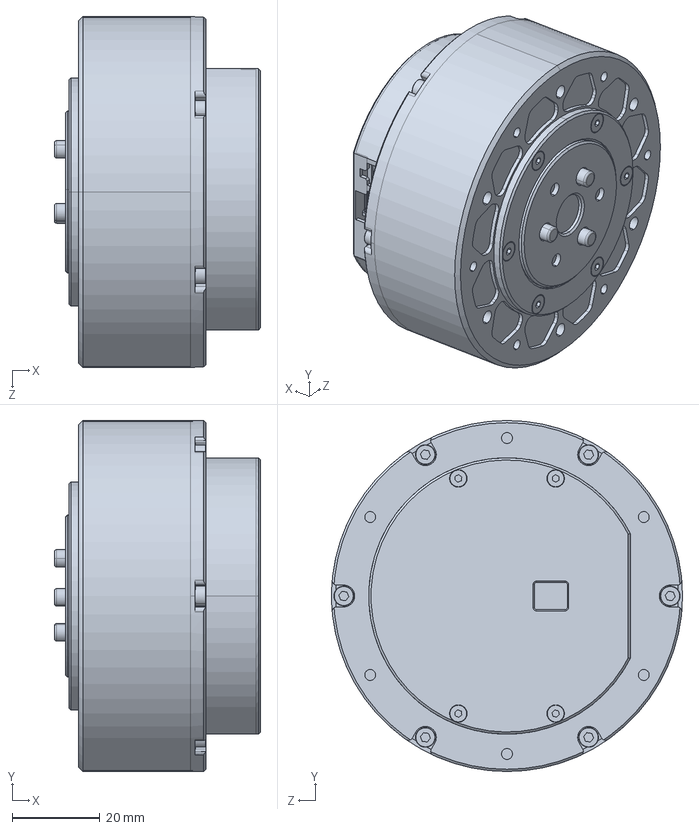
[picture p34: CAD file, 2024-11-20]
Mec/balance/electronic/MG6012-i8.SLDPRT
47.0 x 80.0 x 80.0 mm

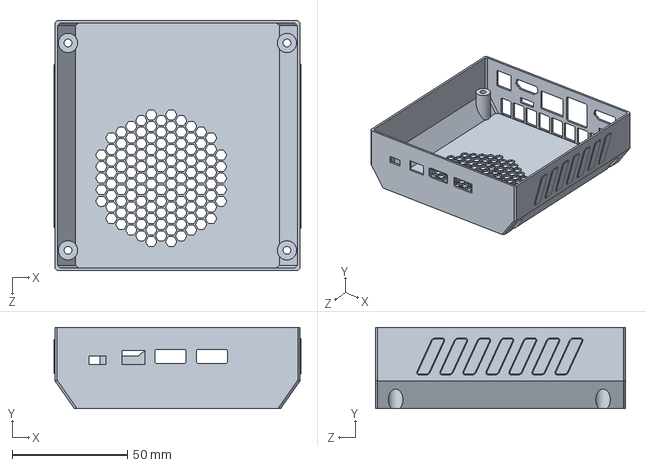
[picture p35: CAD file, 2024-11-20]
Mec/balance/nuc/NUC12WSB保护.SLDPRT
107.2 x 35.2 x 108.6 mm

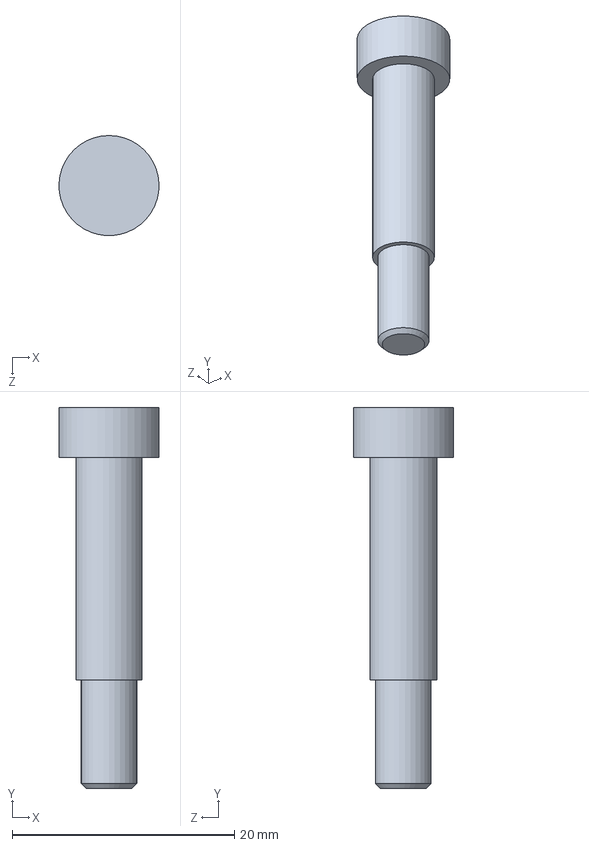
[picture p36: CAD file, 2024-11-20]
Mec/balance/toolbox/d6-l20-塞打.SLDPRT
8.99 x 34.2 x 8.99 mm

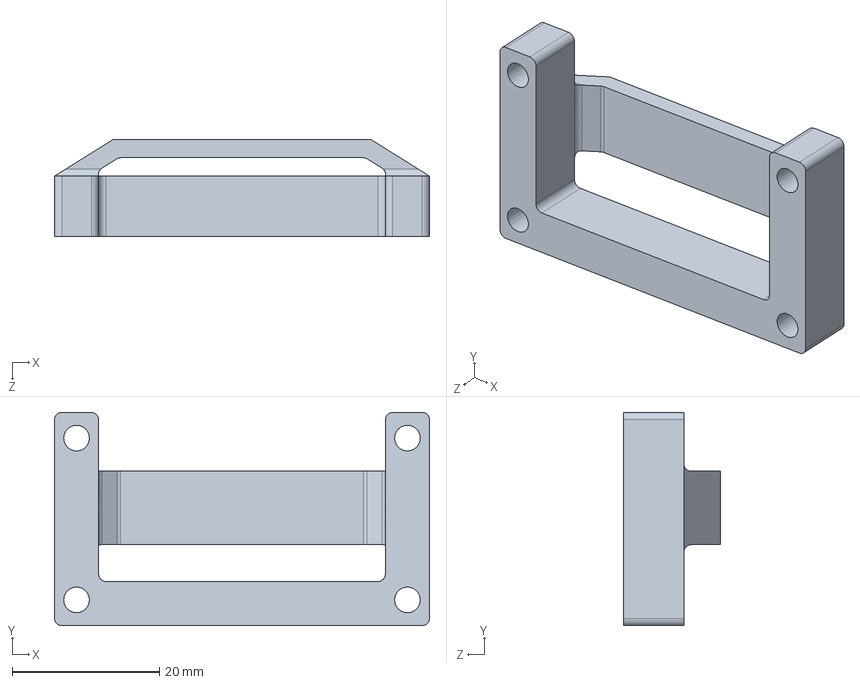
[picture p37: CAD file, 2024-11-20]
Mec/balance/打印件/电池垫件-左.SLDPRT
51.0 x 29.0 x 13.2 mm

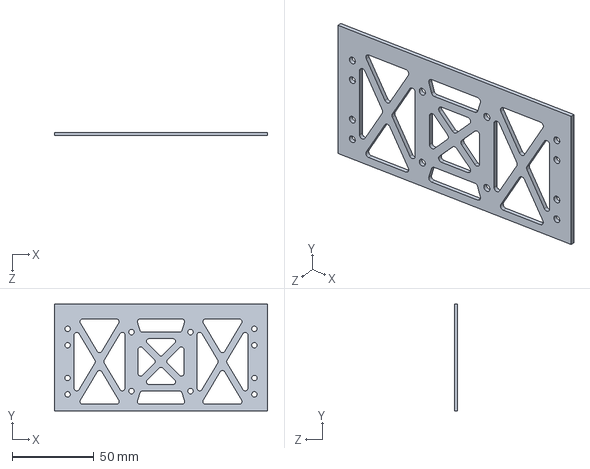
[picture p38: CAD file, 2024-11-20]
Mec/balance/板材/front_bottom.SLDPRT
130.0 x 65.0 x 2.00 mm

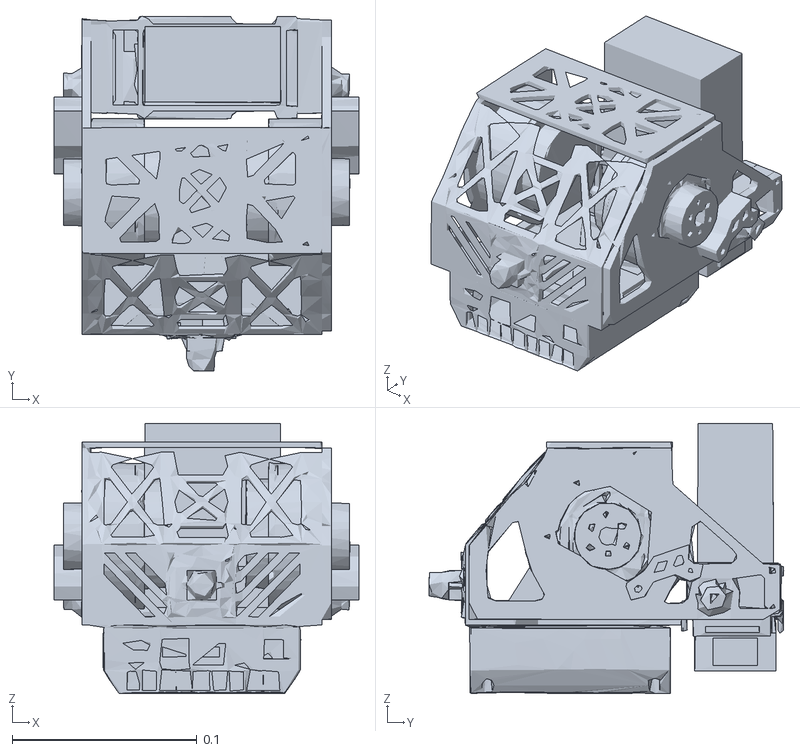
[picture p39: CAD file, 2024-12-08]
Simulation/webots/stl/base.STL
0.165 x 0.192 x 0.146

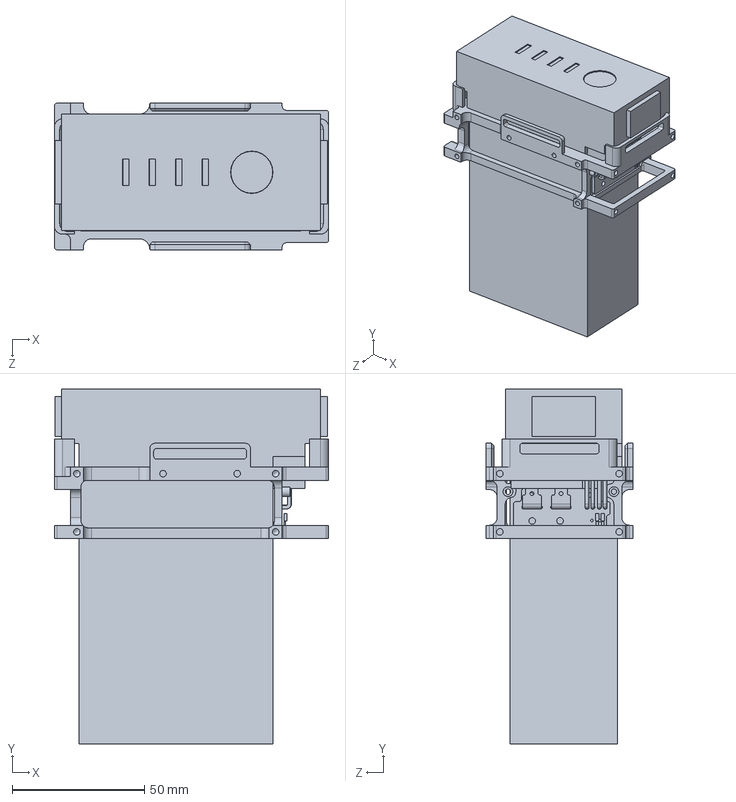
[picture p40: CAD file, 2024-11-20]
Mec/balance/electronic/电池&架.SLDPRT
103.5 x 134.0 x 55.4 mm

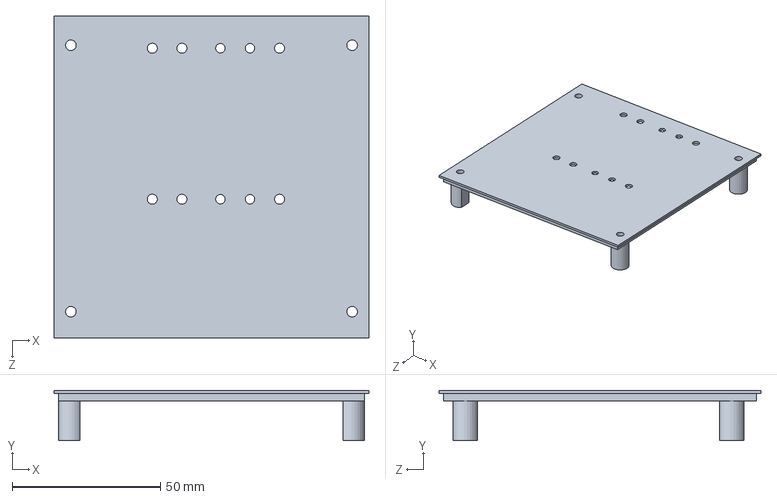
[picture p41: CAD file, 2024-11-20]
Mec/balance/nuc/NUC12保护顶盖.SLDPRT
106.4 x 16.9 x 108.6 mm

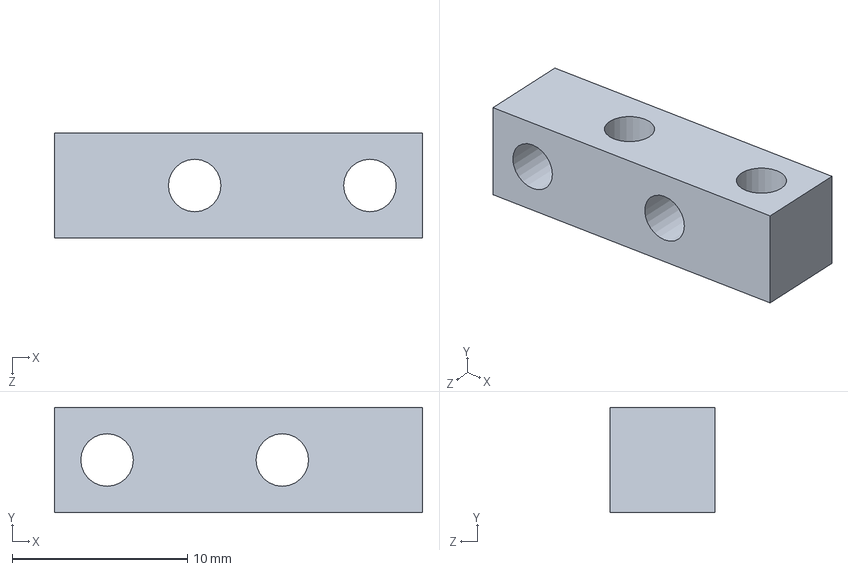
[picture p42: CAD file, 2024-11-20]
Mec/balance/toolbox/长21转接件.SLDPRT
21.0 x 6.00 x 6.00 mm

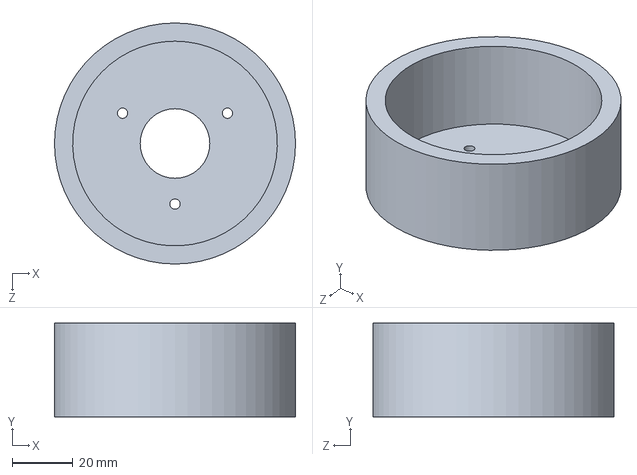
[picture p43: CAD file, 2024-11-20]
Mec/balance/打印件/轮毂.SLDPRT
79.6 x 31.0 x 79.6 mm

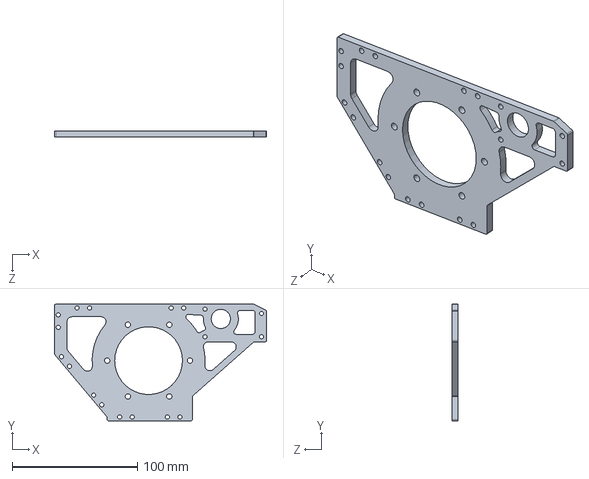
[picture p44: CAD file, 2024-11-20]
Mec/balance/板材/侧板.SLDPRT
169.0 x 93.0 x 5.00 mm

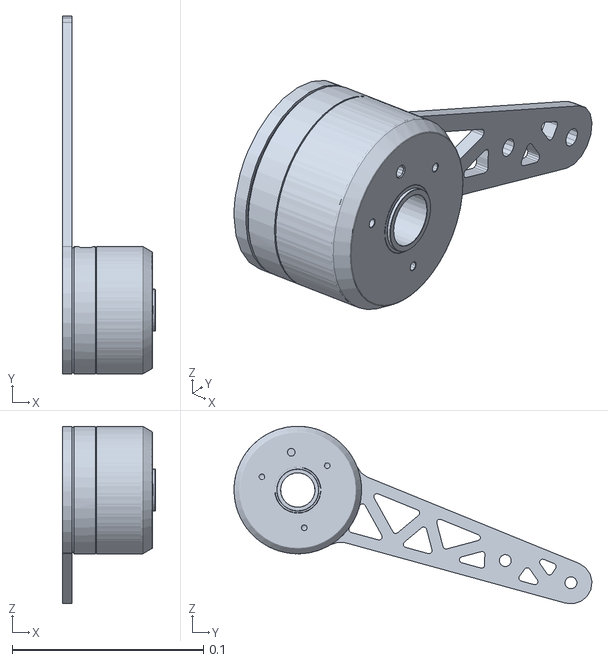
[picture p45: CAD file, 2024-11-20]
Simulation/webots/stl/右大腿.STL
0.0485 x 0.187 x 0.0928

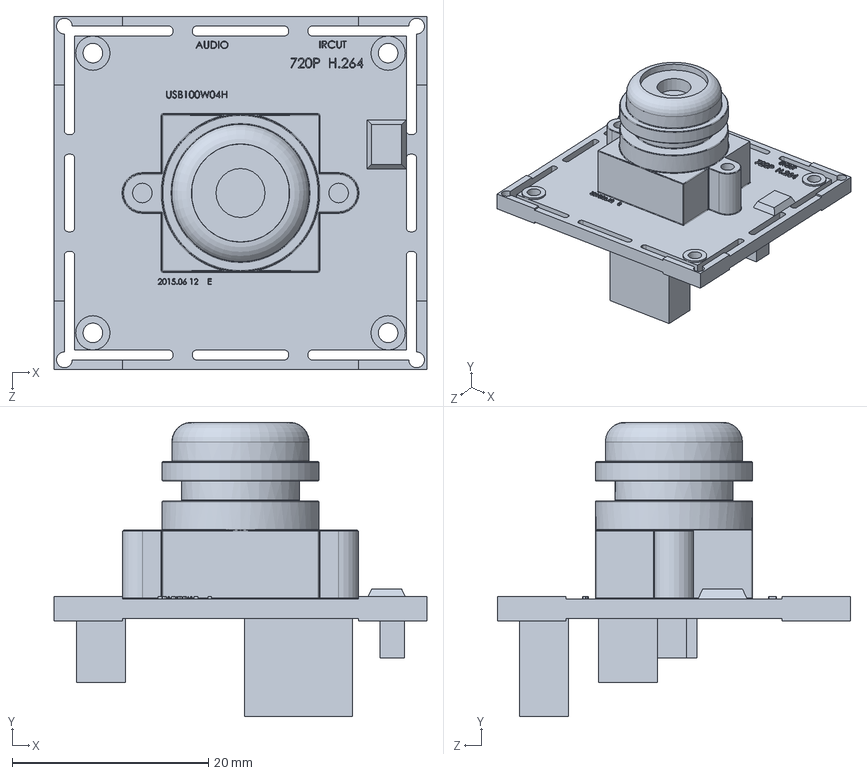
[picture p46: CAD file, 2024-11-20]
Mec/balance/camera/Part1.SLDPRT
38.0 x 30.0 x 36.0 mm

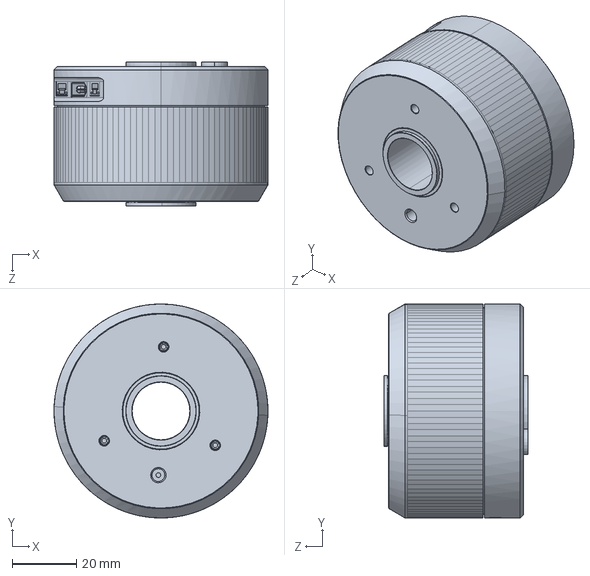
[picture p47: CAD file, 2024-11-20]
Mec/balance/electronic/Alliance配件-电机6020.SLDPRT
66.7 x 66.7 x 45.0 mm

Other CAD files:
Mec/balance/camera/Assem1cam.SLDASM
Mec/balance/camera/Part2.sldprt
Mec/balance/toolbox/防松螺母.SLDPRT
Mec/balance/打印件/限位块.SLDPRT
Mec/balance/toolbox/6-16-2垫片.SLDPRT
Mec/balance/toolbox/F696zz.SLDPRT
Mec/balance/toolbox/d6-l10-塞打.SLDPRT
Mec/balance/toolbox/推力球6_14_5.SLDPRT
Mec/balance/打印件/推力球垫件.SLDPRT
Mec/balance/打印件/电机垫件.SLDPRT
Mec/balance/打印件/电池垫件-右.SLDPRT
Mec/balance/板材/base.SLDPRT
Mec/balance/板材/front.SLDPRT
Mec/balance/板材/leg_l1.SLDPRT
Mec/balance/板材/leg_l2.SLDPRT
Mec/balance/板材/leg_l3.SLDPRT
Mec/balance/板材/top.SLDPRT
Simulation/webots/stl/右主动腿.STL
Simulation/webots/stl/右小腿.STL
Simulation/webots/stl/左主动腿.STL
Simulation/webots/stl/左大腿.STL
Simulation/webots/stl/左小腿.STL
Simulation/webots/stl/轮毂.STL

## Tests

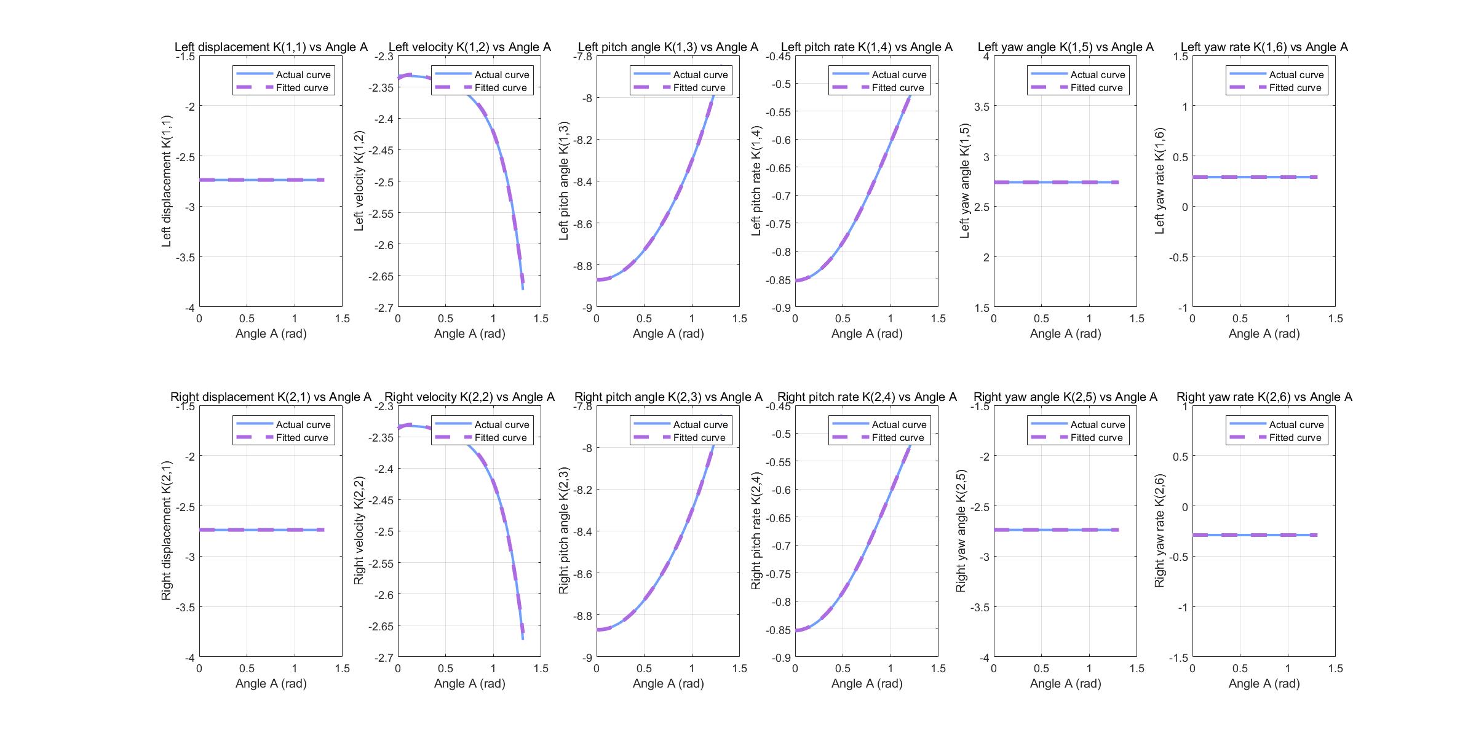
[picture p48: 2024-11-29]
Code/Matlab/Data_and_Graph/Figure/fitting_result.png

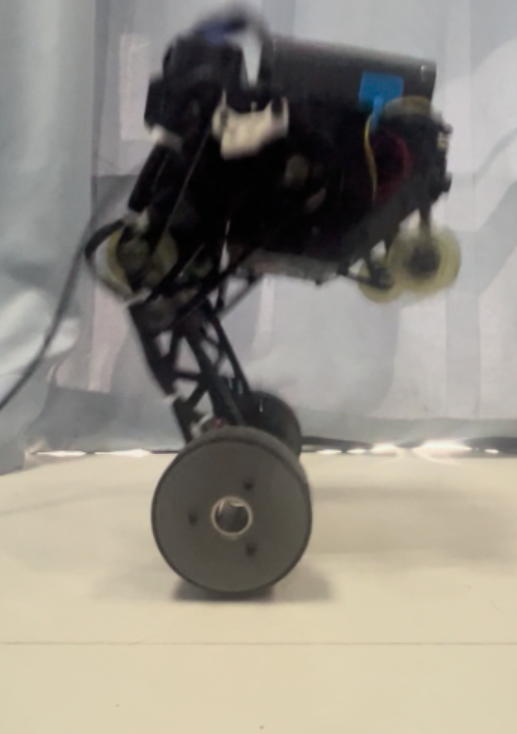
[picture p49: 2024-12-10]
Test_Video/Pictures/jump_1png.png

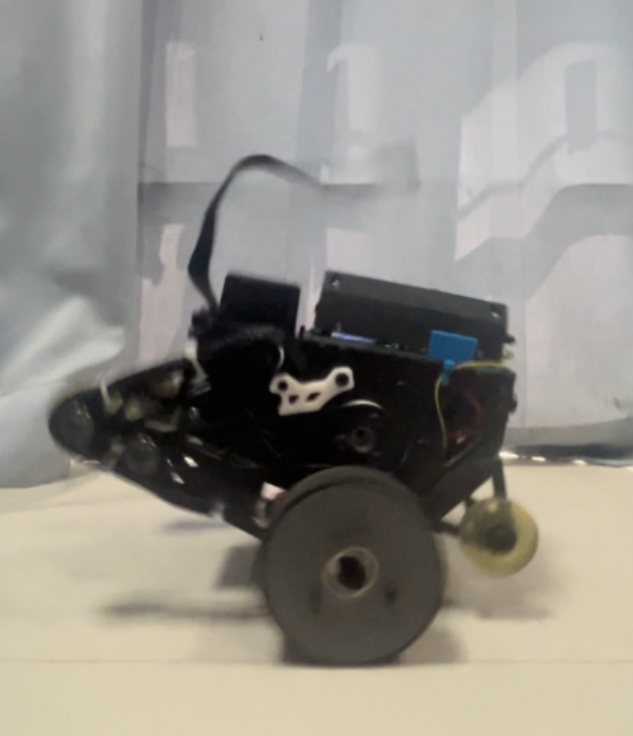
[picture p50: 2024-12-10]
Test_Video/Pictures/jump_3.png

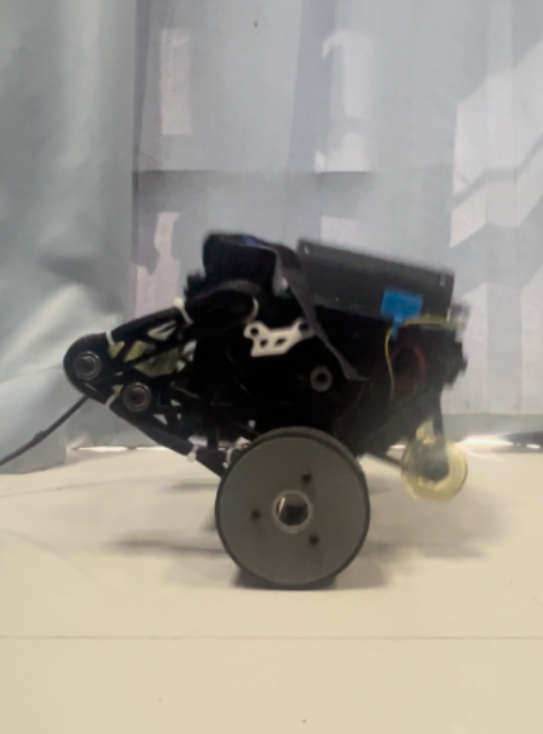
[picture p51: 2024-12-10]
Test_Video/Pictures/jump_0.png

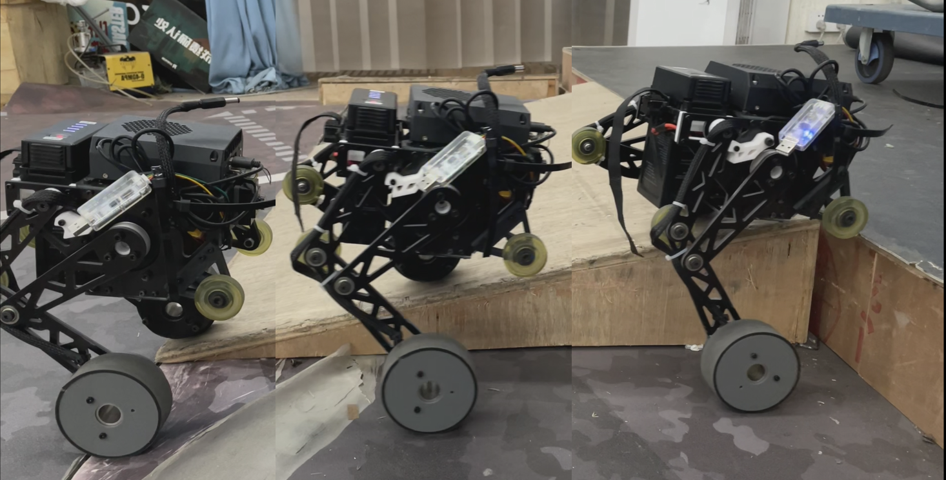
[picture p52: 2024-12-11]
Test_Video/Pictures/roll_test_mirrored.png

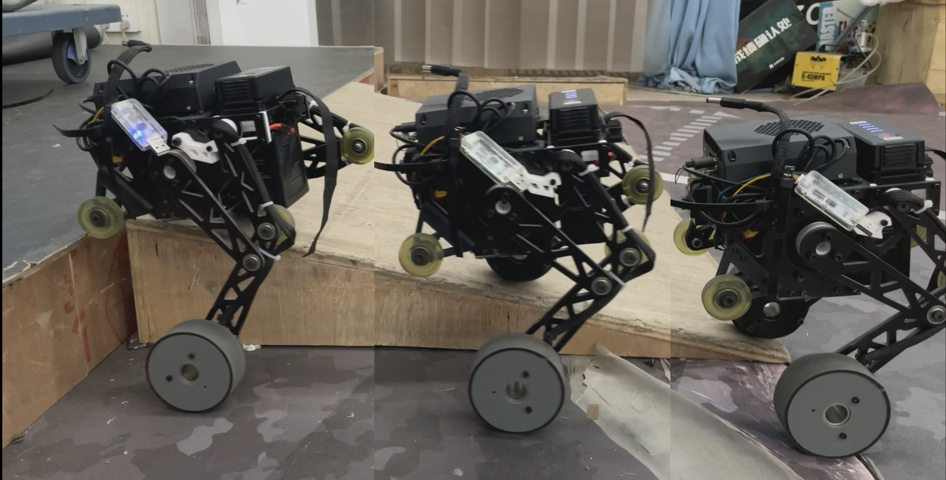
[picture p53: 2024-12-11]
Test_Video/Pictures/roll_test.png

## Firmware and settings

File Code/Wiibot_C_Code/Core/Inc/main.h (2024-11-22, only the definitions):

#define CS1_ACCEL_Pin GPIO_PIN_4
#define CS1_ACCEL_GPIO_Port GPIOA
#define INT1_ACCEL_Pin GPIO_PIN_4
#define INT1_ACCEL_GPIO_Port GPIOC
#define INT1_ACCEL_EXTI_IRQn EXTI4_IRQn
#define INT1_GRYO_Pin GPIO_PIN_5
#define INT1_GRYO_GPIO_Port GPIOC
#define INT1_GRYO_EXTI_IRQn EXTI9_5_IRQn
#define CS1_GYRO_Pin GPIO_PIN_0
#define CS1_GYRO_GPIO_Port GPIOB
#define CS1_ACCEL_Pin GPIO_PIN_4
#define CS1_ACCEL_GPIO_Port GPIOA
#define INT1_ACCEL_Pin GPIO_PIN_4
#define INT1_ACCEL_GPIO_Port GPIOC
#define INT1_ACCEL_EXTI_IRQn EXTI4_IRQn
#define INT1_GRYO_Pin GPIO_PIN_5
#define INT1_GRYO_GPIO_Port GPIOC
#define INT1_GRYO_EXTI_IRQn EXTI9_5_IRQn
#define CS1_GYRO_Pin GPIO_PIN_0
#define CS1_GYRO_GPIO_Port GPIOB

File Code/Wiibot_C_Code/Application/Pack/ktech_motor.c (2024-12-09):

#include "ktech_motor.h"

/*有待完善：

电机离线数据处理，如角度和

*/


#define _9025_TORQUE_CONSTANT     0.32f	  //9025转矩常数，单位：N*m/A 32f
#define _8016_TORQUE_CONSTANT			0.24f		//8016转矩常数，单位：N*m/A
#define _6012_TORQUE_CONSTANT     1.09f   //6012转矩常数，单位：N*m/A
#define _9025_MAX_CURRENT         16.f    //9025输出最大电流，手册-16.5~16.5
#define _8016_MAX_CURRENT         32.f    //8016输出最大电流，手册-33~33
#define _6012_MAX_CURRENT         14.f    //8016输出最大电流，手册-33~33

/**
  * @brief          将电机接收原始电流数据转为实际转矩
  * @param[in]      Motor_Ktech_t *motor     电机本体
  * @retval         none
  */
static void Raw_Current_to_Torque(Motor_Ktech_t *motor);

/**
  * @brief          将电机期望输出扭矩转为原始电流数据,用于发送数据的处理
  * @param[in]      Motor_Ktech_t *motor     电机本体
  * @retval         none
  */
static void Torque_to_Raw_Current(Motor_Ktech_t *motor);

/**
  * @brief          将编码器值转化为弧度制，并计算电机角度和
  * @param[in]      Motor_Ktech_t *motor     电机本体
  * @retval         none
  */
static void Encoder_to_Motor_Angle(Motor_Ktech_t *motor);

/**
  * @brief          计算电机旋转角度和
  * @param[in]      Motor_Ktech_t *motor     电机本体
  * @retval         none
  */
static void Angle_Sum_Cal(Motor_Ktech_t *motor);

/**
  * @brief          >>电机组控制专用<<将电机期望输出扭矩转为原始电流数据,用于发送数据的处理
  * @param[in]      Motor_Ktech_t *motor     电机本体
  * @retval         none
  */
static void Group_Torque_to_Raw_Current(Motor_Ktech_t *motor);

/**
  * @brief          单电机读取状态1，包括电机温度，电压，错误标志位
  * @param[in]      Motor_Ktech_t *motor     电机本体
  * @retval         none
  */
static void Single_Motor_Read_State_1(Motor_Ktech_t *motor);

/**
  * @brief          单电机设置PID参数到RAM 0 ROM 1
  * @param[in]      Motor_Ktech_t *motor     电机本体
  * @retval         none
  */
static void Single_Motor_Set_PI(Motor_Ktech_t *motor, uint8_t type);


/**
  * @brief          向电机发送指令请求获得电机信息，会给数组第一个位赋值,内含发送操作
  * @param[in]      Motor_Ktech_t *motor     电机本体
  * @param[in]      uint8_t command         请求命令
  * @retval         none
  */
void Motor_Pull_Request(Motor_Ktech_t *motor, uint8_t command)
{
    memset(motor->tx_info->single_tx_buff, 0, 8);

    switch(command)
    {
        case TORQUE_CLOSE_LOOP_ID://返回电机温度，转矩，速度
            motor->tx_info->single_tx_buff[0] = TORQUE_CLOSE_LOOP_ID;
            break;
        case ENCODER_RX_ID://返回编码器三个值
            motor->tx_info->single_tx_buff[0] = ENCODER_RX_ID;
            break;
        case MOTOR_ANGLE_ID://返回总角度 int64_t
            motor->tx_info->single_tx_buff[0] = MOTOR_ANGLE_ID;
            break;
        default:
            break;
    }
		
		CAN_SendData(motor->born_info->hcan, motor->born_info->stdId, motor->tx_info->single_tx_buff);
		
		memset(motor->tx_info->single_tx_buff, 0, 8);
}

/**
  * @brief          电机CAN中断接收数据处理
  * @param[in]      Motor_Ktech_t *motor      电机本体
  * @param[in]      uint8_t *rxBuf						CAN接收数据包
  * @retval         none
  */
void Motor_Get_Info(Motor_Ktech_t *motor, uint8_t *rxBuf)
{
	uint8_t command_bit = rxBuf[0];
	
	switch(command_bit)
	{
		case TORQUE_CLOSE_LOOP_ID://返回电机温度，转矩电流，速度,编码器位置
				motor->rx_info->temperature = rxBuf[1];
		
				motor->rx_info->torque_current_raw = rxBuf[3];
				motor->rx_info->torque_current_raw <<= 8;
				motor->rx_info->torque_current_raw |= rxBuf[2];
		    Raw_Current_to_Torque(motor);
		
				motor->rx_info->speed = rxBuf[5];
				motor->rx_info->speed <<= 8;
				motor->rx_info->speed |= rxBuf[4];
		
				motor->rx_info->encoder = rxBuf[7];//类似6020云台，
				motor->rx_info->encoder <<= 8;
				motor->rx_info->encoder |= rxBuf[6];
				Encoder_to_Motor_Angle(motor);
		
          break;
    case ENCODER_RX_ID://返回编码器三个值
			  motor->rx_info->encoder_raw = rxBuf[5];
		    motor->rx_info->encoder_raw <<= 8;
		    motor->rx_info->encoder_raw |= rxBuf[4];
		
				motor->rx_info->encoder_offset = rxBuf[7];
		    motor->rx_info->encoder_offset <<= 8;
		    motor->rx_info->encoder_offset |= rxBuf[6];
        break;
    case MOTOR_ANGLE_ID://返回总角度 int64_t
        break;
		case STATE1_ID:
			  motor->rx_info->temperature = rxBuf[1];
		    motor->rx_info->voltage = (uint16_t)((rxBuf[3]<<8)|rxBuf[2]);
//		    motor->rx_info->voltage <<= 8;
//        motor->rx_info->voltage |= rxBuf[3];		
			  motor->rx_info->error_state = rxBuf[7];
//			  motor->rx_info->voltage_state = 0x01 && motor->rx_info->error_state;
//		    motor->rx_info->temper_state = 0x08 && motor->rx_info->error_state;
			  break;
		case PID_RX_ID:
			  motor->rx_info->angle_PID_Kp = rxBuf[2];
		    motor->rx_info->angle_PID_Ki = rxBuf[3];
				motor->rx_info->speed_PID_Kp = rxBuf[4];
		    motor->rx_info->speed_PID_Ki = rxBuf[5];
				motor->rx_info->torque_PID_Kp = rxBuf[6];
		    motor->rx_info->torque_PID_Ki = rxBuf[7];
			  break;
		case PID_TX_RAM_ID:
			  motor->rx_info->angle_PID_Kp = rxBuf[2];
		    motor->rx_info->angle_PID_Ki = rxBuf[3];
				motor->rx_info->speed_PID_Kp = rxBuf[4];
		    motor->rx_info->speed_PID_Ki = rxBuf[5];
				motor->rx_info->torque_PID_Kp = rxBuf[6];
		    motor->rx_info->torque_PID_Ki = rxBuf[7];
			  break;
    default:
        break;
	}
}

/**
  * @brief          单电机控制输出转矩,含有CAN发送操作
  * @param[in]      Motor_Ktech_t *motor     电机本体
  * @retval         none
  */
void Motor_Set_Torque(Motor_Ktech_t *motor)
{
	  if(motor != NULL)
		{
			  Torque_to_Raw_Current(motor);
	
		    motor->tx_info->single_tx_buff[0]    = TORQUE_CLOSE_LOOP_ID; //扭矩闭环控制
		    motor->tx_info->single_tx_buff[1]    = 0x00;
		    motor->tx_info->single_tx_buff[2]    = 0x00;
        motor->tx_info->single_tx_buff[3]    = 0x00;
        motor->tx_info->single_tx_buff[4]    = (uint8_t) (motor->tx_info->torque_current_raw);
        motor->tx_info->single_tx_buff[5]    = (uint8_t) (motor->tx_info->torque_current_raw >> 8);
		    motor->tx_info->single_tx_buff[6]    = 0x00;
        motor->tx_info->single_tx_buff[7]    = 0x00;
		    
		    CAN_SendData(motor->born_info->hcan, motor->born_info->stdId, motor->tx_info->single_tx_buff);
		    
		    memset(motor->tx_info->single_tx_buff,0,8);
		}
}

/**
  * @brief          单电机卸力
  * @param[in]      Motor_Ktech_t *motor     电机本体
  * @retval         none
  */
void Single_Motor_Sleep(Motor_Ktech_t *motor)
{
	if(motor != NULL)
	{
		  motor->tx_info->single_tx_buff[0]    = TORQUE_CLOSE_LOOP_ID; //扭矩闭环控制
		  
		  memset(&motor->tx_info->single_tx_buff[1],0,7);
		  
		  CAN_SendData(motor->born_info->hcan, motor->born_info->stdId, motor->tx_info->single_tx_buff);
	}
}
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

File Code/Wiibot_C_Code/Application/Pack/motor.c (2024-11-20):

/*
*	RP MOTOR_BAG
*	2022.11.6 
* AUTHOR CCB HXZP
*
*使用电机前必须配置好电机的类型、id号、驱动方式,以及初始化函数指针motor_class_init
*使用pid前也需要进行pid初始化，否则无法使用
*可以直接使用内置函数进行pid控制 也可以直接使用库内定义函数或者自己定义的函数
*kt系列电机：使用kt系列电机前需要先实例化motor_9025_info_t，再与motor内的指针联系，其余步骤无异
*/

#include "motor.h"




/**
 *	@brief	电机发送信息
 */
uint8_t can_tx_buff(struct motor_class_t *motor, int16_t *buff,uint8_t len)
{
	uint8_t res;
	
	if(motor->id.motor_type > 0 && motor->id.motor_type <= 3)
	{
		
	}
	
	return res;
}

/**
 *	@brief	电机接收信息
 */
uint8_t can_rx_buff(struct motor_class_t *motor, uint8_t *buff,uint8_t len)
{
	uint8_t res;
	
	if(motor == NULL || buff == NULL)
	{
		return 0;
	}
	
	if(motor->state.init_flag == M_DEINIT)
	{
		return 0;	
	}
	
	if(motor->id.motor_type > 0 && motor->id.motor_type <= 3)
	{
		get_rm_info(motor,buff);
	}
	else if(motor->id.motor_type > 3 && motor->id.motor_type <= 5)
	{
		get_kt_9025_info(motor,buff);
	}
	
	return res;
}


















/**
 *	@brief	电机pid初始化
 */
void motor_class_pid_init(struct motor_pid *pid, float *buff)
{
	if(pid == NULL || buff == NULL)
	{
		return;
	}
	
	pid->info.target   = 0;
	pid->info.measure  = 0;	
	pid->info.err      = 0;	
	pid->info.last_err = 0;
	pid->info.integral = 0;
	pid->info.pout     = 0;
	pid->info.iout     = 0;
	pid->info.dout     = 0;	
	pid->info.out      = 0;		
	
	pid->set.kp           = buff[0];
	pid->set.ki           = buff[1];	
	pid->set.kd           = buff[2];
	pid->set.blind_err    = buff[3];
	pid->set.integral_max = buff[4];
	pid->set.iout_max     = buff[5];	
	pid->set.out_max      = buff[6];
	
	pid->info.init_flag = M_INIT;
	
}	

/**
 *	@brief	电机初始化
 */
void motor_class_init(struct motor_class_t *motor)
{
	if(motor == NULL)
	{
		return;
	}

	if(motor->id.motor_type == KT9025 && motor->kt9025_info == NULL)
	{
		return;
	}
	
	motor->state.work_state = M_OFFLINE;
	
	motor->state.offline_cnt = 0;
	motor->state.offline_cnt_max = 100;	
	

	if(motor->id.drive_type == M_CAN1 || motor->id.drive_type == M_CAN2)
	{
		get_rm_can_drvie(motor);
	}
	else if(motor->id.drive_type == M_USART1 || motor->id.drive_type == M_USART2)
	{

	}	
	
	motor->pid_init     = motor_class_pid_init;
	motor->heartbeat    = motor_class_heartbeat;	
	
	motor->c_stuck_flag = motor_class_stucking_flag;
	motor->c_offset     = motor_offset;
	motor->c_judge_dir  = motor_judge_dir;
	
	motor->c_speed = motor_pid_speed;
	motor->c_angle = motor_pid_angle;
	motor->c_posit = motor_pid_position;	
	
	motor->c_pid1 = motor_pid_single;
	motor->c_pid2 = motor_pid_double;		
	
	motor->state.init_flag = M_INIT;
}

/**
 *	@brief	电机心跳
 */
void motor_class_heartbeat(struct motor_class_t *motor)
{
	if(motor == NULL)
	{
		return;
	}

	if(motor->state.init_flag == M_DEINIT)
	{
		return;	
	}
	
	motor->state.offline_cnt++;
	
	if(motor->state.offline_cnt > motor->state.offline_cnt_max) 
	{
		motor->state.offline_cnt = motor->state.offline_cnt_max;
		motor->state.work_state = M_OFFLINE;
	}
	else 
	{
		if(motor->state.work_state == M_OFFLINE)
			motor->state.work_state = M_ONLINE;
	}
}

/**
*	@brief	堵转判断：仅是必要条件，并不是一定堵住 torque_limit:扭矩阈值 return:1为是 0为否 

用户进行函数修改，特供给限位和拨盘，速度和位置，1速度，2位置
 */
uint8_t motor_class_stucking_flag(struct motor_class_t *motor, uint8_t pid_type, float err_limit, uint16_t lock_cnt_max)
{
	uint8_t res = 0;
	
	
	if(motor->state.init_flag == M_DEINIT || motor->state.work_state == M_OFFLINE)return 0;	
	
	/*速度pid的堵转判断*/
	if(pid_type == 1)
	{
		if(m_abs(motor->pid.speed.info.err) > err_limit && m_abs(motor->rx_info.speed) < 30)//30是2006，5是3508
	  { 
	  	motor->base_info.lock_cnt++;
		
		  if (motor->base_info.lock_cnt == lock_cnt_max)
			  res = 1;
		  else
			  res = 0;
	  }
	  else
	  {
		  res = 0;
		  motor->base_info.lock_cnt = 0;
  	}
	}
	
	/*位置pid的堵转判断*/
	if(pid_type == 2)
	{
		if(m_abs(motor->pid.position.info.err) > err_limit && m_abs(motor->rx_info.speed) < 5)
	  { 
	  	motor->base_info.lock_cnt++;
		
		  if (motor->base_info.lock_cnt == lock_cnt_max)
			  res = 1;
		  else
			  res = 0;
	  }
	  else
	  {
		  res = 0;
		  motor->base_info.lock_cnt = 0;
  	}
	}
	
	
	
	return res;
	
}

/*-----------------------------------------------------------------
*数据处理
-----------------------------------------------------------------*/
/**
 *	@brief	周期处理 tar：源数据 cycle:数据范围
 */
float motor_cycle(float tar,float cycle)
{
	if(tar < 0)          tar += cycle;
	else if(tar >=cycle) tar -= cycle;
	
	return tar;
}
/**
 *	@brief	过半圈处理 angle：源数据 cycle:数据范围
 */
float motor_half_cycle(float angle,float max)
{
	if(m_abs(angle) > (max/2))
	{	
		if(angle >= 0)
			angle += -max;		
		else
			angle +=  max;
	}
	return angle;
}
/**
 *	@brief	计算电机方向  limit:电机数据范围
 */
void motor_judge_dir(struct motor_class_t *motor,uint16_t range)
{
	int16_t angle = 0;
	
	if(motor->rx_info.angle < motor->mec_info.mec_mid)
		 angle = motor->rx_info.angle - motor->mec_info.mec_mid + range;
	else
	   angle = motor->rx_info.angle - motor->mec_info.mec_mid;

	if(m_abs(angle - range/2) < range/4)
	{
		motor->mec_info.dir = MOTOR_B;
	}
	else 
	{
		motor->mec_info.dir = MOTOR_F;
	}	
}
/**
 *	@brief	对电机角度做偏置 类如yaw轴电机朝向，原始朝前为1777，修改后朝前为0 
 *            limit:电机数据范围
 */
void motor_offset(struct motor_class_t *motor, uint16_t range)
{
	motor_rx_info_t *info = &motor->rx_info;
	
	int16_t angle = 0;
	
	if(info->angle < motor->mec_info.mec_mid)
		 angle = info->angle - motor->mec_info.mec_mid + range;
	else
	   angle = info->angle - motor->mec_info.mec_mid;
	
  angle = -angle + range + range/4;
	
	if(angle > range)angle = angle - range;

	angle = motor_cycle(angle - range/4,range);
	
	info->angle_offset = angle;			
}


/*-----------------------------------------------------------------
*电机pid
-----------------------------------------------------------------*/

/**
 *	@brief	获取误差 tar - mea
 */
float motor_pid_err(motor_pid_t *pid,float measure)
{
	motor_pid_info_t *pid_info = &pid->info;
	
	if(pid->info.init_flag == M_DEINIT)
	{
		return 0;
	}
	
	pid_info->measure = measure;
	pid_info->err = pid_info->target - pid_info->measure;
	return pid_info->err;

}

/**
 *	@brief	pid计算 不包含err计算
 */
float motor_pid_cal(motor_pid_t *pid)
{
	
	if(pid->info.init_flag == M_DEINIT)
	{
		return 0;
	}
	
	motor_pid_info_t *pid_info = &pid->info;
	motor_pid_set_t  *pid_set = &pid->set;	
	
	//保存误差值(需要在外面自行计算误差)
	//pid->err = err;
	if(m_abs(pid_info->err)<=(pid_set->blind_err))
		pid_info->err = 0;
	
	//积分
	pid_info->integral += pid_info->err;
	pid_info->integral = m_constrain(pid_info->integral, -pid_set->integral_max, +pid_set->integral_max);
	
	//pid 输出项计算
	pid_info->pout = pid_set->kp * pid_info->err;
	pid_info->iout = pid_set->ki * pid_info->integral;
	pid_info->dout = pid_set->kd * (pid_info->err - pid_info->last_err);
	
	pid_info->iout = m_constrain(pid_info->iout, -pid_set->iout_max, pid_set->iout_max);	
	//累加pid输出值
	pid_info->out = pid_info->pout + pid_info->iout + pid_info->dout;
	pid_info->out = m_constrain(pid_info->out, -pid_set->out_max, pid_set->out_max);

	pid_info->last_err = pid_info->err;
	
	return pid_info->out;
}
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

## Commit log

2024-11-20 电机通讯，陀螺仪原始数据及解算完成
    [6-16-2垫片.SLDPRT, Alliance配件-电机6020.SLDPRT, Assem1cam.SLDASM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]
2024-11-22 加了遥控器的代码，可以通讯。陀螺仪部分因为磁力计yaw难处理，lqr控制不太行，会在平衡点附近抖动
    [rm.cfg]
2024-11-22 陀螺仪在换解算后没问题，程序运行时间没问题，现在启动时角度收敛较慢，参数未整定好
    [rm.cfg]
2024-11-25 solve imu slow init problem
    [my_robot.c, my_robot.h, my_task.c]
2024-11-26 加入位移控制，重心靠后有大问题
2024-11-26 加配重后效果好很多，改了一下在matlab中的机体质量参数，发现yaw目标值需要处理一下
2024-11-26 处理了yaw目标值，yaw的控制正常
2024-11-26 加了关节电机部分代码，弧度目标值赋值有点问题
2024-11-27 sd control added, ready to try double pid control
2024-11-27 腿长控制加入双极pid，参数未整定好
2024-11-27 调了两级pid的参，花了很短时间调出来的效果就很好，现在在崩溃那jb五连杆为什么没有这样搞
2024-11-27 加了roll轴双极pid控制
2024-11-28 完成K矩阵关于腿长关系代码
2024-11-29 完成matlab拟合代码，得到多项式系数
    [Will_data.xlsx]
2024-11-30 加了拟合代码，有点问题
    [Will_data.xlsx]
2024-12-08 收到小电脑串口数据
    [Will_data.xlsx, base.STL]
2024-12-09 roll length pid ok, graph ok
    [Leg_length.csv, Will_data.xlsx, distance_and_pitch.csv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]
2024-12-09 加了简单的离地检测
    [off_ground.csv]
2024-12-10 加跳跃，并测得数据。数据测量还差roll
    [jump.csv]
2024-12-11 vision motion added, roll test graph finished
    [go_up_hill.csv, roll.csv]
2024-12-13 equ ok
    [Will_data.xlsx]

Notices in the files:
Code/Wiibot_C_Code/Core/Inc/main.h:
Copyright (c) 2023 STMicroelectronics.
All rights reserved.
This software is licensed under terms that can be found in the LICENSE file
